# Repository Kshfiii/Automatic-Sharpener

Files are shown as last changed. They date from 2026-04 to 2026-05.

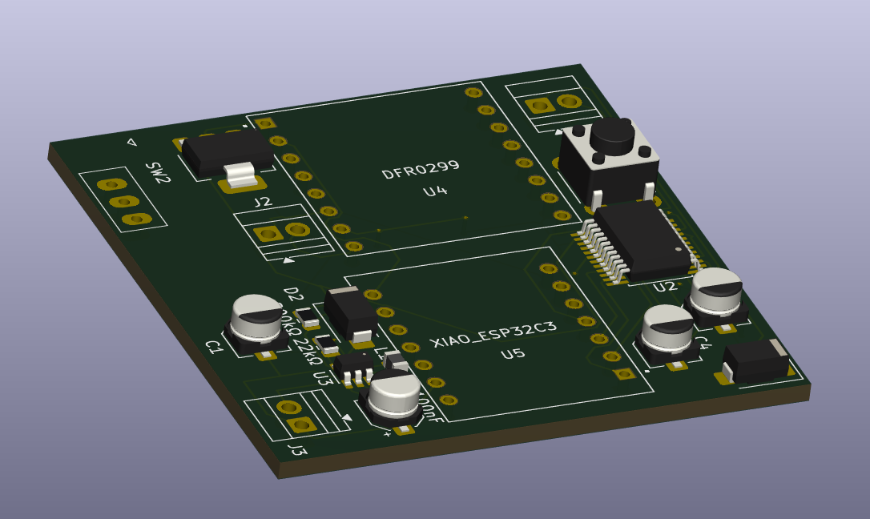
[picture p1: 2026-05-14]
PCB/hdhdh.PNG

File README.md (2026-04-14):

Project

# Da Sharpener
A custom automatic pencil sharpener built around the Seeed Studio XIAO ESP32-C3. It spins an N20 DC motor to sharpen your pencil at the press of a button, and plays Chipi Chipi Chapa Chapa every single time. Because why not.

# About
This is a fully self-contained pencil sharpener with onboard LiPo charging, a boost-converted 6V motor supply, and a DFPlayer Mini for audio playback on a custom 48mm  PCB.
I built this because I wanted to get into PCB design using chips, so that I can confidently use them instead of dev boards in my future projects, all while making something fun and functional. On the hardware side, this project introuced me to audio functions and components.

# Project Snippets



Capture
****

# Assembly
To assemble the project open [Onshape](https://cad.onshape.com/documents/c32b9fc8cbec21775e9ce121/w/f4af039bfc6de04a7036ff46/e/f9eacd1e50641cdce73afd8e) In the 'Parts' tab, all parts have been labelled. Now open the Assembly and follow along. Put the assembled PCB between Part 1 and Part 2 and close them together. Put the motor in the rectangle placeholder in Part 2 and cover it with Part 3. After that, Attach Part 3 on the shaft of the motor. attach a sharpner on the underside of Part 4 and then attach Part 4 to Part 3. Lastly, attach Part 6 to the top of Part 3. All of this can be seen in the assembly. If confusion persists, you may contact me at: kasshafemman@gmail.com 

# Usage & Features

  1. Charge via the USB-C port on the XIAO ESP32-C3
  2. Power on using the slide switch
  3. Insert pencil into the sharpener
  4. Hold the tactile switch — motor spins and sharpening begins
  5. Chipi Chipi Chapa Chapa plays through the onboard speaker
  6. Release the switch — motor stops
  7. Take out round cartilage to clean, then insert it back

# Hardware Note — Power Architecture
Attach lipo batter to GND and BATT+ pins on the underside of the Esp32. 

# Firmware Files
Files and their functions:

sharpener.ino — Main loop, switch debounce, motor and audio control
config.h — Pin definitions and settings

# Component List

  1. Seeed Studio XIAO ESP32-C3
  2. TB6612FNG Motor Driver IC
  3. MT3608 Boost Converter IC
  4. AMS1117-5.0 LDO Regulator
  5. N20 DC Gear Motor (6V)
  6. DFPlayer Mini (YX5200)
  7. 8Ω 1W Speaker
  8. Tactile Switch
  9. 3.7V LiPo Battery
  10. MicroSD Card

## Bill of Materials
| Component | Quantity | Est. Cost (USD) | Purchase Links | 
| :--- | :---: | :--- | :--- |
| **Seeed Studio XIAO ESP32-C**| 1 | $11.50 |[Link](https://www.aliexpress.com/item/1005009855437801.html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) | 
| **TB6612FNG Motor Driver IC**| 1 | $1.00 | [Link](https://www.aliexpress.com/item/1005004242795745.html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) | 
| **MT3608 Boost Converter IC** | 1 | $1.20 | [Link](https://www.aliexpress.com/item/1005008853748359.html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) | 
| **AMS1117-5.0 LDO Regulator** | 1 | $2.50 | [Link](https://www.aliexpress.com/item/1005002487704059.html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) | 
| **N20 DC Gear Motor (6V)** | 1 | $2.12 | [Link](https://www.aliexpress.com/item/1005002008404532.html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 ) | 
| **MicroSD Card** | 1 | $7.68 | [Link](https://www.aliexpress.com/item/1005007498167692.html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) | 
| **8Ω 1W Speaker** | 1 | $1.70 | [Link](https://www.aliexpress.com/item/1005008660223571.html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) | 
| **Tactile Switch** | 1 | $0.50 | [Link](https://digilog.pk/products/12-x-12mm-x-7-5mm-push-button-in-pakistan-en?variant=44490991370518 )| 
| **PCB** | 1 | $5.00 | [Link](https://jlcpcb.com/)| 
| **DFPlayer Mini** | 1 | $5.50 | [Link](https://www.aliexpress.com/item/1005011540339952.html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)| 
| **Total Build Cost:** |  | **~$35.00** |

#
Happy Building :)

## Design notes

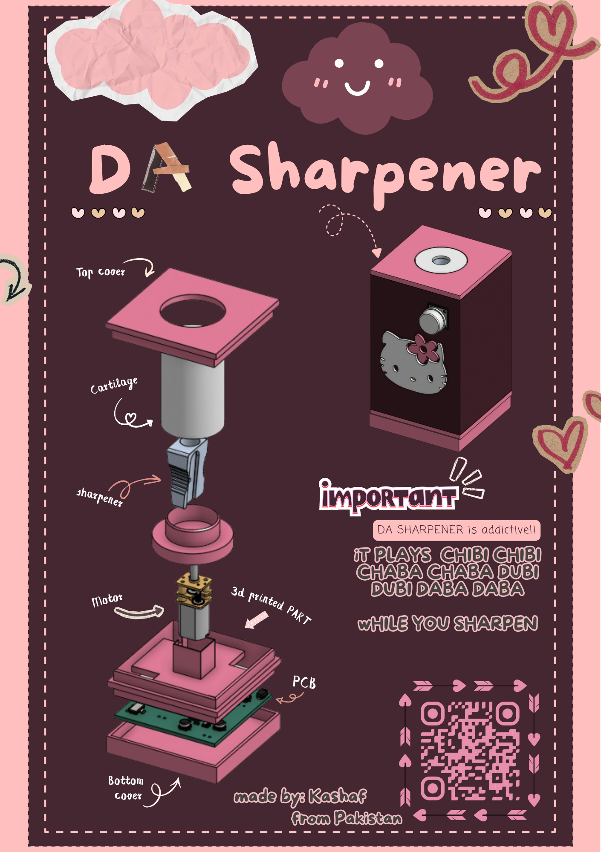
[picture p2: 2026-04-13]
Da Sharpener.png

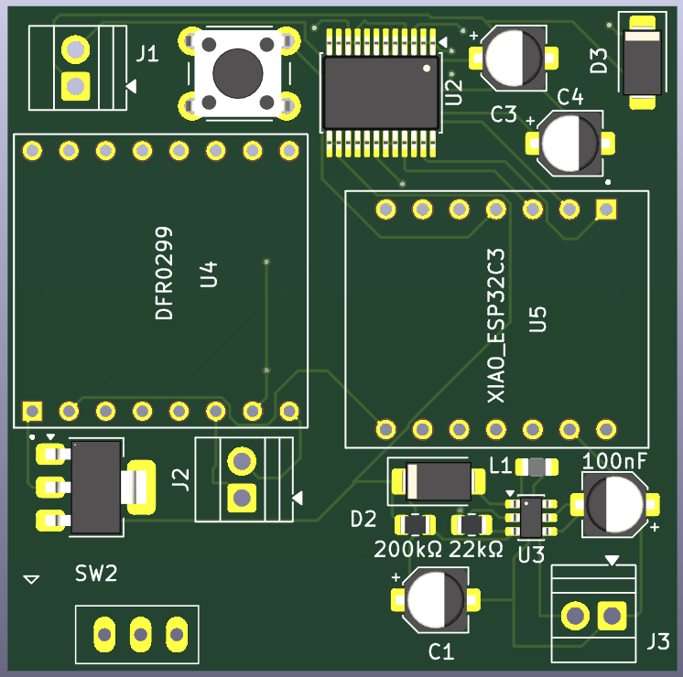
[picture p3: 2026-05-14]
PCB/Capture.PNG

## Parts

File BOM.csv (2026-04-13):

Component | Quantity | Est. Cost (USD) | Purchase Links
Seeed Studio XIAO ESP32-C | 1 | $11.50 | https://www.aliexpress.com/item/1005009855437801.html?mp=1
TB6612FNG Motor Driver IC | 1 | $1.00 | https://www.aliexpress.com/item/1005004242795745.html?mp=1
MT3608 Boost Converter ICl | 1 | $1.20 | https://www.aliexpress.com/item/1005008853748359.html?mp=1
AMS1117-5.0 LDO Regulator | 1 | $2.50 | https://www.aliexpress.com/item/1005002487704059.html?curPageLogUid=jNloBkgONfbe
N20 DC Gear Motor (6V) | 1 | $2.12 | https://www.aliexpress.com/item/1005002008404532.html?mp=1
MicroSD Card | 1 | $7.68 | https://www.aliexpress.com/item/1005007498167692.html?mp=1
8Ω 1W Speaker | 1 | $1.70 | https://www.aliexpress.com/item/1005008660223571.html?mp=1
Tactile Switch | 1 | $0.50 | https://digilog.pk/products/12-x-12mm-x-7-5mm-push-button-in-pakistan-en?variant=44490991370518
PCB | 1 | $5.00 | https://jlcpcb.com/
DFPlayer Mini | 1 | $5.50 | https://www.aliexpress.com/item/1005011540339952.html?mp=1
Total Build Cost: |  | ~$35.00

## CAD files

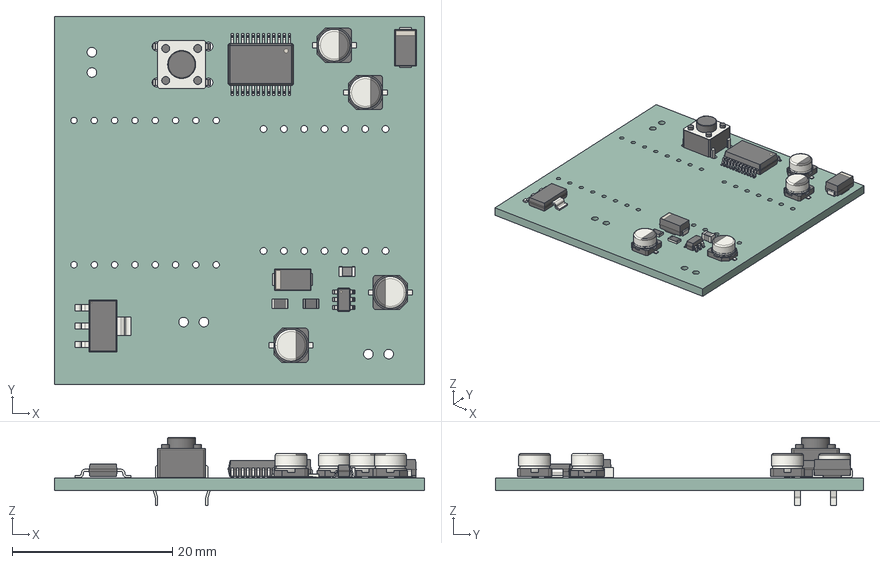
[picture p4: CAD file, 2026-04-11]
PCB/PCB_sharpener.step
46.3 x 46.0 x 8.50 mm
CP_Elec_4x3 x 4
D_SMA x 2
SSOP-24_5.3x8.2mm_P0.65mm
SOT-223
SOT-23-6
SW_PUSH_6mm_H5mm
R_0805_2012Metric x 2
L_0805_2012Metric
PCB_sharpener_PCB

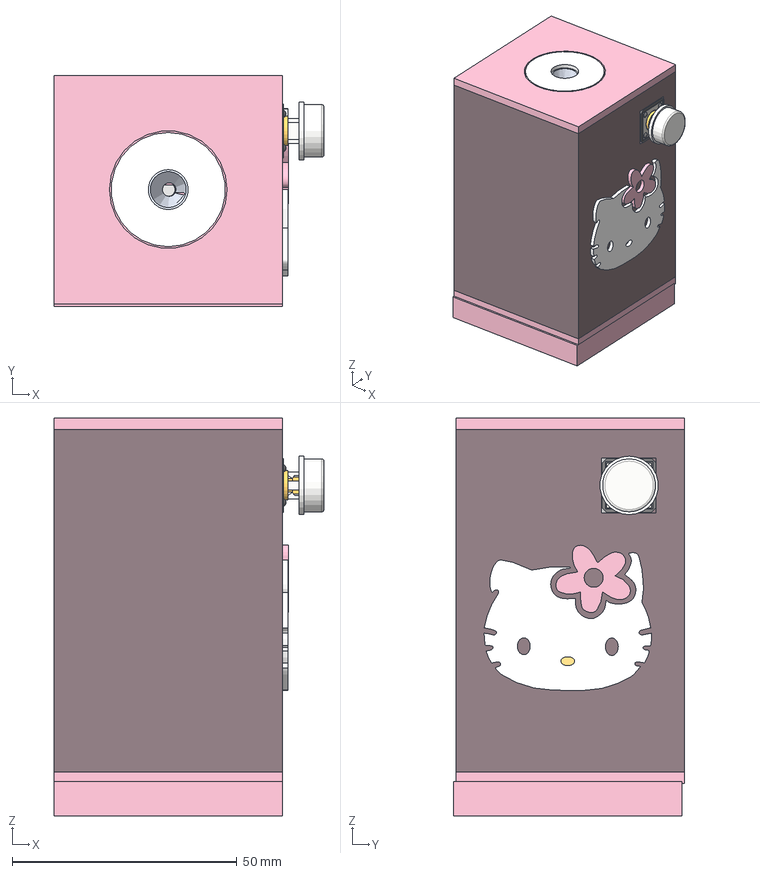
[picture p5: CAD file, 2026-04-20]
Sharpener.step
60.0 x 51.4 x 88.5 mm
OMRON B3F-4050 12x12 switch v1 x 8
CP_Elec_4x3 x 4
D_SMA x 2
SW_PUSH_6mm_H5mm
SOT-23-6
SSOP-24_5.3x8.2mm_P0.65mm
L_0805_2012Metric
SOT-223
R_0805_2012Metric x 2
PCB_sharpener_PCB
Gear Box x 8
Motor
Shaft

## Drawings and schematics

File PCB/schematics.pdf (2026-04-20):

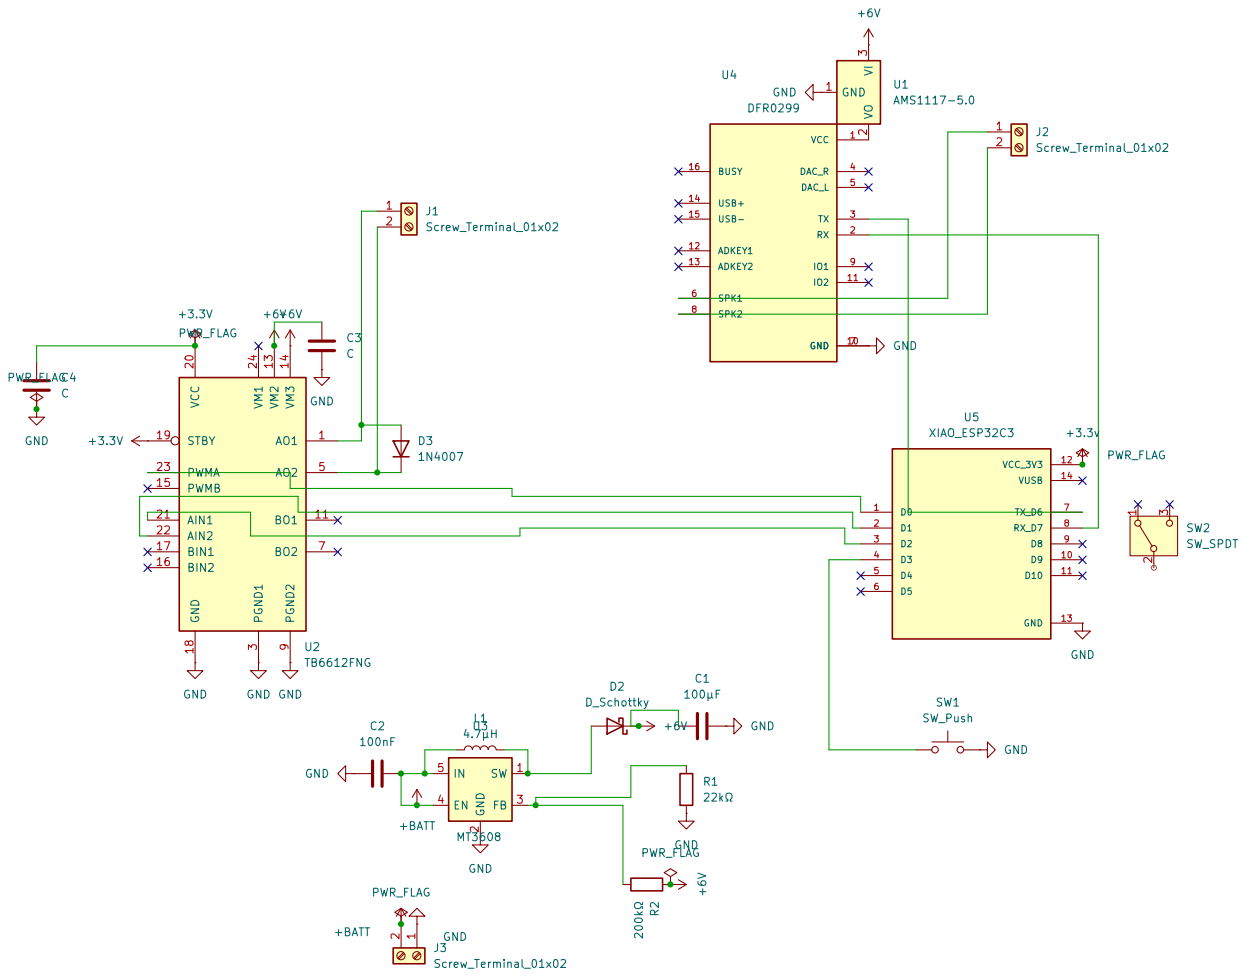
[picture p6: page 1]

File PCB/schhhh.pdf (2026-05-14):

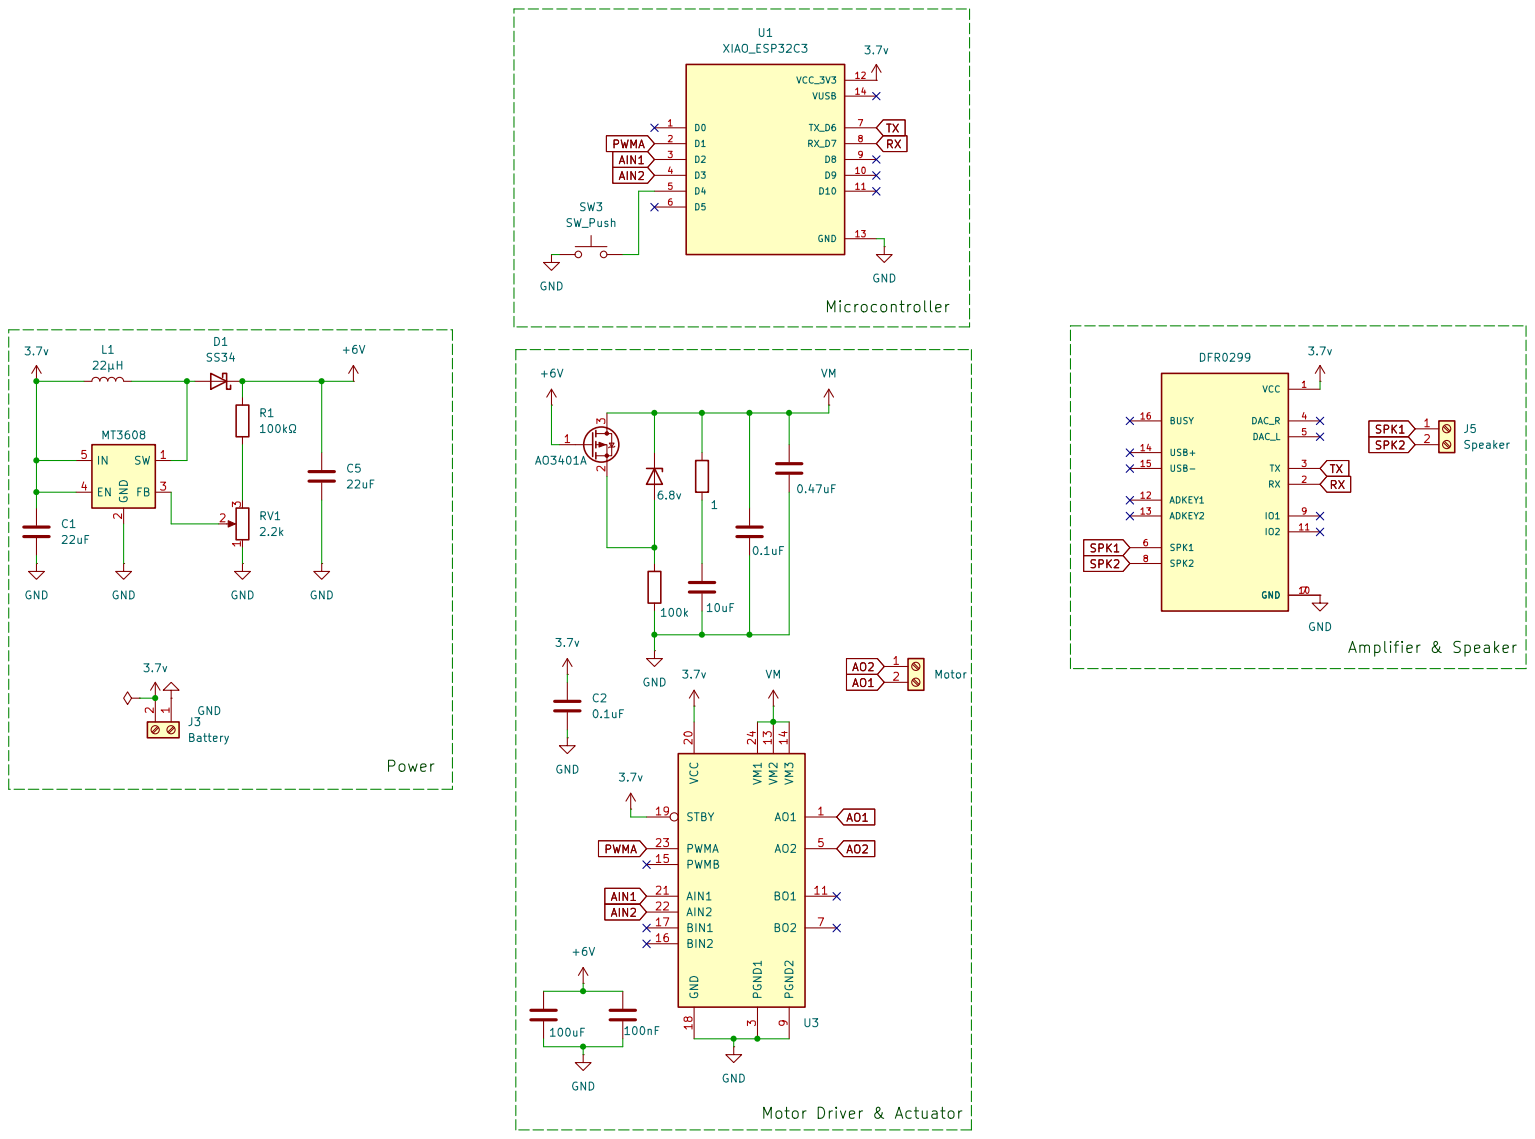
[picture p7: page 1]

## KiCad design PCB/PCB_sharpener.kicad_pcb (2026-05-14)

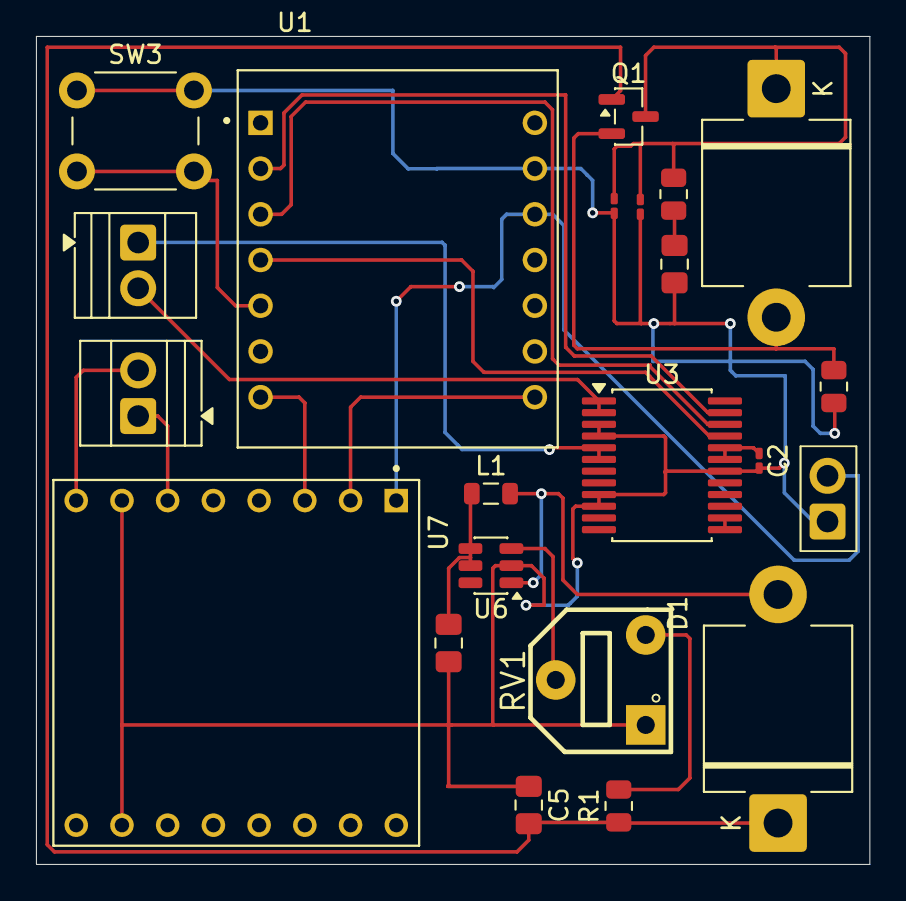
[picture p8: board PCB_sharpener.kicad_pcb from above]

Board: 2 copper layers, 46.3 x 46.0 mm, 22 parts (0 on the bottom side), 19 nets.

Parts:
C1, C5: 22uF; C_0805_2012Metric_Pad1.18x1.45mm_HandSolder
C2, C9: 0.1uF; C_0201_0603Metric_Pad0.64x0.40mm_HandSolder
C8: 10uF; C_0805_2012Metric_Pad1.18x1.45mm_HandSolder
C10: 0.47uF; C_0201_0603Metric_Pad0.64x0.40mm_HandSolder
D1: SS34; D_5KPW_P12.70mm_Horizontal
D2: 6.8v; D_5KPW_P12.70mm_Horizontal
J3: Battery; TerminalBlock_Xinya_XY308-2.54-2P_1x02_P2.54mm_Horizontal
J4: Motor; TerminalBlock_Xinya_XY308-2.54-2P_1x02_P2.54mm_Horizontal
J5: Speaker; TerminalBlock_Xinya_XY308-2.54-2P_1x02_P2.54mm_Horizontal
L1: 22µH; L_0805_2012Metric
Q1: AO3401A; SOT-23
R1: 100kΩ; R_0805_2012Metric
R2: 100k; R_0805_2012Metric
R3: 1; R_0805_2012Metric
RV1: 2.2k; MP
SW3: SW_Push; SW_PUSH_6mm_H5mm
U1: XIAO_ESP32C3; MODULE_XIAO_ESP32C3
U3: TB6612FNG; SSOP-24_5.3x8.2mm_P0.65mm
U6: MT3608; SOT-23-6
U7: DFR0299; MODULE_DFR0299

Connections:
3.7v: C1.2, C2.1, J3.2, L1.1, U1.12 (VCC_3V3), U3.19 (STBY), U3.20 (VCC), U6.4 (EN), U6.5 (IN), U7.1 (VCC)
+6V: C5.2, D1.1 (K), Q1.1 (G), R1.1
AIN1: U1.3 (D2), U3.22 (AIN2)
AIN2: U1.4 (D3), U3.21 (AIN1)
AO1: J4.2, U3.1 (AO1), U3.2 (AO1)
AO2: J4.1, U3.5 (AO2), U3.6 (AO2)
GND: C1.1, C2.2, C5.1, C8.2, C9.2, C10.2, J3.1, R2.2, RV1.1, SW3.1, U1.13 (GND), U3.3 (PGND1), U3.4 (PGND1), U3.9 (PGND2), U3.10 (PGND2), U3.18 (GND), U6.2 (GND), U7.7 (GND), U7.10 (GND)
unnamed: C8.1, R3.2
unnamed: D1.2 (A), L1.2, U6.1 (SW)
unnamed: D2.2 (A), Q1.2 (S), R2.1
unnamed: R1.2, RV1.3
unnamed: SW3.2, U1.5 (D4)
unnamed: RV1.2, U6.3 (FB)
PWMA: U1.2 (D1), U3.23 (PWMA)
RX: U1.8 (RX_D7), U7.2 (RX)
SPK1: J5.1, U7.6 (SPK1)
SPK2: J5.2, U7.8 (SPK2)
TX: U1.7 (TX_D6), U7.3 (TX)
VM: C9.1, C10.1, D2.1 (K), Q1.3 (D), R3.1, U3.13 (VM2), U3.14 (VM3), U3.24 (VM1)

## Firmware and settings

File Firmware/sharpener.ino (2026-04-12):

#include <Arduino.h>
#include <HardwareSerial.h>
#include <DFRobotDFPlayerMini.h>
#include "config.h"

HardwareSerial dfSerial(1);
DFRobotDFPlayerMini player;

bool motorRunning = false;
bool lastButtonState = HIGH;
unsigned long lastDebounce = 0;

void motorOn() {
  digitalWrite(AIN1, HIGH);
  digitalWrite(AIN2, LOW);
  analogWrite(PWMA, MOTOR_SPEED);
}

void motorOff() {
  digitalWrite(AIN1, LOW);
  digitalWrite(AIN2, LOW);
  analogWrite(PWMA, 0);
}

void setup() {
  pinMode(PWMA, OUTPUT);
  pinMode(AIN1, OUTPUT);
  pinMode(AIN2, OUTPUT);
  pinMode(BUTTON, INPUT_PULLUP);

  dfSerial.begin(9600, SERIAL_8N1, DF_RX, DF_TX);
  player.begin(dfSerial);
  player.volume(25);

  motorOff();
}

void loop() {
  bool buttonState = digitalRead(BUTTON);

  if (buttonState != lastButtonState) {
    lastDebounce = millis();
  }

  if (millis() - lastDebounce > DEBOUNCE_MS) {
    if (buttonState == LOW && !motorRunning) {
      motorOn();
      player.play(1);
      motorRunning = true;
    }

    if (buttonState == HIGH && motorRunning) {
      motorOff();
      player.stop();
      motorRunning = false;
    }
  }

  lastButtonState = buttonState;
}

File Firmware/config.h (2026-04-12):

#pragma once

#define PWMA  2
#define AIN1  3
#define AIN2  4
#define BUTTON 5

#define DF_RX 20
#define DF_TX 21

#define MOTOR_SPEED 255
#define DEBOUNCE_MS 50

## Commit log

2026-04-13 Update BOM.csv format to standard CSV
    [BOM.csv]
2026-04-13 Update total build cost format in BOM.csv
    [BOM.csv]
